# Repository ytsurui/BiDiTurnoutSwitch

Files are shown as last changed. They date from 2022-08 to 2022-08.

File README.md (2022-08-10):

# BiDi Turnout Switch

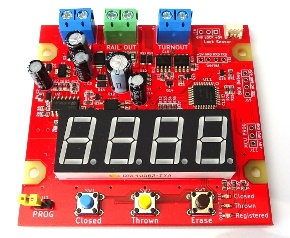
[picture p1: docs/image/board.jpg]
PCB Preview


NMRA DCC 規格のうち、BiDi (RailCom) によって送信される車両のアドレス情報を利用して、接続されているポイント線路を自動的に転換することが可能な装置です。

本リポジトリには、基板設計データとファームウェアが含まれます。

## 開発環境

- KiCad Version (5.1.12)-1
- Microchip Studio Version 7.0.2542

## 各種ドキュメント

  * [パーツリスト](docs/partslist.md)

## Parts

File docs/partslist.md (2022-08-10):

# Parts List

<table>
  <th>
    <td>Name</td>
    <td>Count</td>
  </th>
  <tr>
    <td>C1</td>
    <td>25PK220MEFC6.3X11<br>(220uF 25V)</td>
    <td>1</td>
  </tr>
  <tr>
    <td>C2, C3, C14</td>
    <td>25PK100MEFC5X11<br>(100uF 25V)</td>
    <td>3</td>
  </tr>
  <tr>
    <td>C12</td>
    <td>25PK470MEFC8X11.5<br>(470uF 25V)</td>
    <td>1</td>
  </tr>
  <tr>
    <td>C4, C11, C13</td>
    <td>GRM155F11E104ZA01<br>(0.1uF 25V 1005)</td>
    <td>3</td>
  </tr>
  <tr>
    <td>C15</td>
    <td>GRM155R11H103KA88<br>(0.01uF 50V 1005)</td>
    <td>1</td>
  </tr>
  <tr>
    <td>D1, D2</td>
    <td>SR54F</td>
    <td>2</td>
  </tr>
  <tr>
    <td>D3-D5</td>
    <td>1N4148W</td>
    <td>3</td>
  </tr>
  <tr>
    <td>D11-D14</td>
    <td>SS2040FL</td>
    <td>4</td>
  </tr>
  <tr>
    <td>D15</td>
    <td>OSL40562-IYA<br>(0.56 Inch Four Digit Display, Common Anode)</td>
    <td>1</td>
  </tr>
  <tr>
    <td>D16</td>
    <td>OSBL1608C1A<br>(Blue SMD LED, 1.6mm x 0.8mm)</td>
    <td>1</td>
  </tr>
  <tr>
    <td>D17</td>
    <td>OSYL1608C1A<br>(Yellow SMD LED, 1.6mm x 0.8mm</td>
    <td>1</td>
  </tr>
  <tr>
    <td>D18</td>
    <td>OSYG1608C1A<br>(Green SMD LED, 1.6mm x 0.8mm)</td>
    <td>1</td>
  </tr>
  <tr>
    <td>J1, J14</td>
    <td>TB111-2<br>(Screw Terminal, Blue)</td>
    <td>2</td>
  </tr>
  <tr>
    <td>J2</td>
    <td>TB111-2<br>(Screw Terminal, Green)</td>
    <td>1</td>
  </tr>
  <tr>
    <td>J17</td>
    <td>Molex 0530480350</td>
    <td>1</td>
  </tr>
  <tr>
    <td>Q1, Q2</td>
    <td>SSM3K7002BFU</td>
    <td>2</td>
  </tr>
  <tr>
    <td>Q11, Q12</td>
    <td>FDS4897C</td>
    <td>2</td>
  </tr>
  <tr>
    <td>Q13-Q15</td>
    <td>2SC4116</td>
    <td>3</td>
  </tr>
  <tr>
    <td>R1, R2</td>
    <td>3.6 ohm 3.2mm x 2.5mm</td>
    <td>2</td>
  </tr>
  <tr>
    <td>R3, R4</td>
    <td>220 ohm 1.6mm x 0.8mm</td>
    <td>2</td>
  </tr>
  <tr>
    <td>R5</td>
    <td>270k ohm 1.6mm x 0.8mm</td>
    <td>1</td>
  </tr>
  <tr>
    <td>R7</td>
    <td>820 ohm 1.6mm x 0.8mm</td>
    <td>1</td>
  </tr>
  <tr>
    <td>R8</td>
    <td>33k ohm 1.6mm x 0.8mm</td>
    <td>1</td>
  </tr>
  <tr>
    <td>R6, R10, R15, R21, R22<br>R25, R26, R31-R37, R41</td>
    <td>1k ohm 1.6mm x 0.8mm</td>
    <td>15</td>
  </tr>
  <tr>
    <td>R11, R12</td>
    <td>10k ohm 1.6mm x 0.8mm</td>
    <td>2</td>
  </tr>
  <tr>
    <td>R9, R27, R28</td>
    <td>100k ohm 1.6mm x 0.8mm</td>
    <td>3</td>
  </tr>
  <tr>
    <td>R23, R24</td>
    <td>330 ohm 1.6mm x 0.8mm</td>
    <td>2</td>
  </tr>
  <tr>
    <td>R40-R42</td>
    <td>4.7k ohm 1.6mm x 0.8mm</td>
    <td>3</td>
  </tr>
  <tr>
    <td>SW1</td>
    <td>DTS-63-N-V-BLU<br>(Blue Tact Switch)</td>
    <td>1</td>
  </tr>
  <tr>
    <td>SW2</td>
    <td>DTS-63-N-V-YLW<br>(Yellow Tact Switch)</td>
    <td>1</td>
  </tr>
  <tr>
    <td>SW3</td>
    <td>DTS-63-N-V-BLK<br>(Black Tact Switch)</td>
    <td>1</td>
  </tr>
  <tr>
    <td>U1, U12</td>
    <td>NJM78L05UA<br>(5V 100mA)</td>
    <td>2</td>
  </tr>
  <tr>
    <td>U2</td>
    <td>LM339<br>(SOIC14)</td>
    <td>1</td>
  </tr>
  <tr>
    <td>U11</td>
    <td>ATmega808-AU<br>ATmega808-AF</td>
    <td>1</td>
  </tr>
  <tr>
    <td>U13</td>
    <td>TLP2361</td>
    <td>1</td>
  </tr>
</table>

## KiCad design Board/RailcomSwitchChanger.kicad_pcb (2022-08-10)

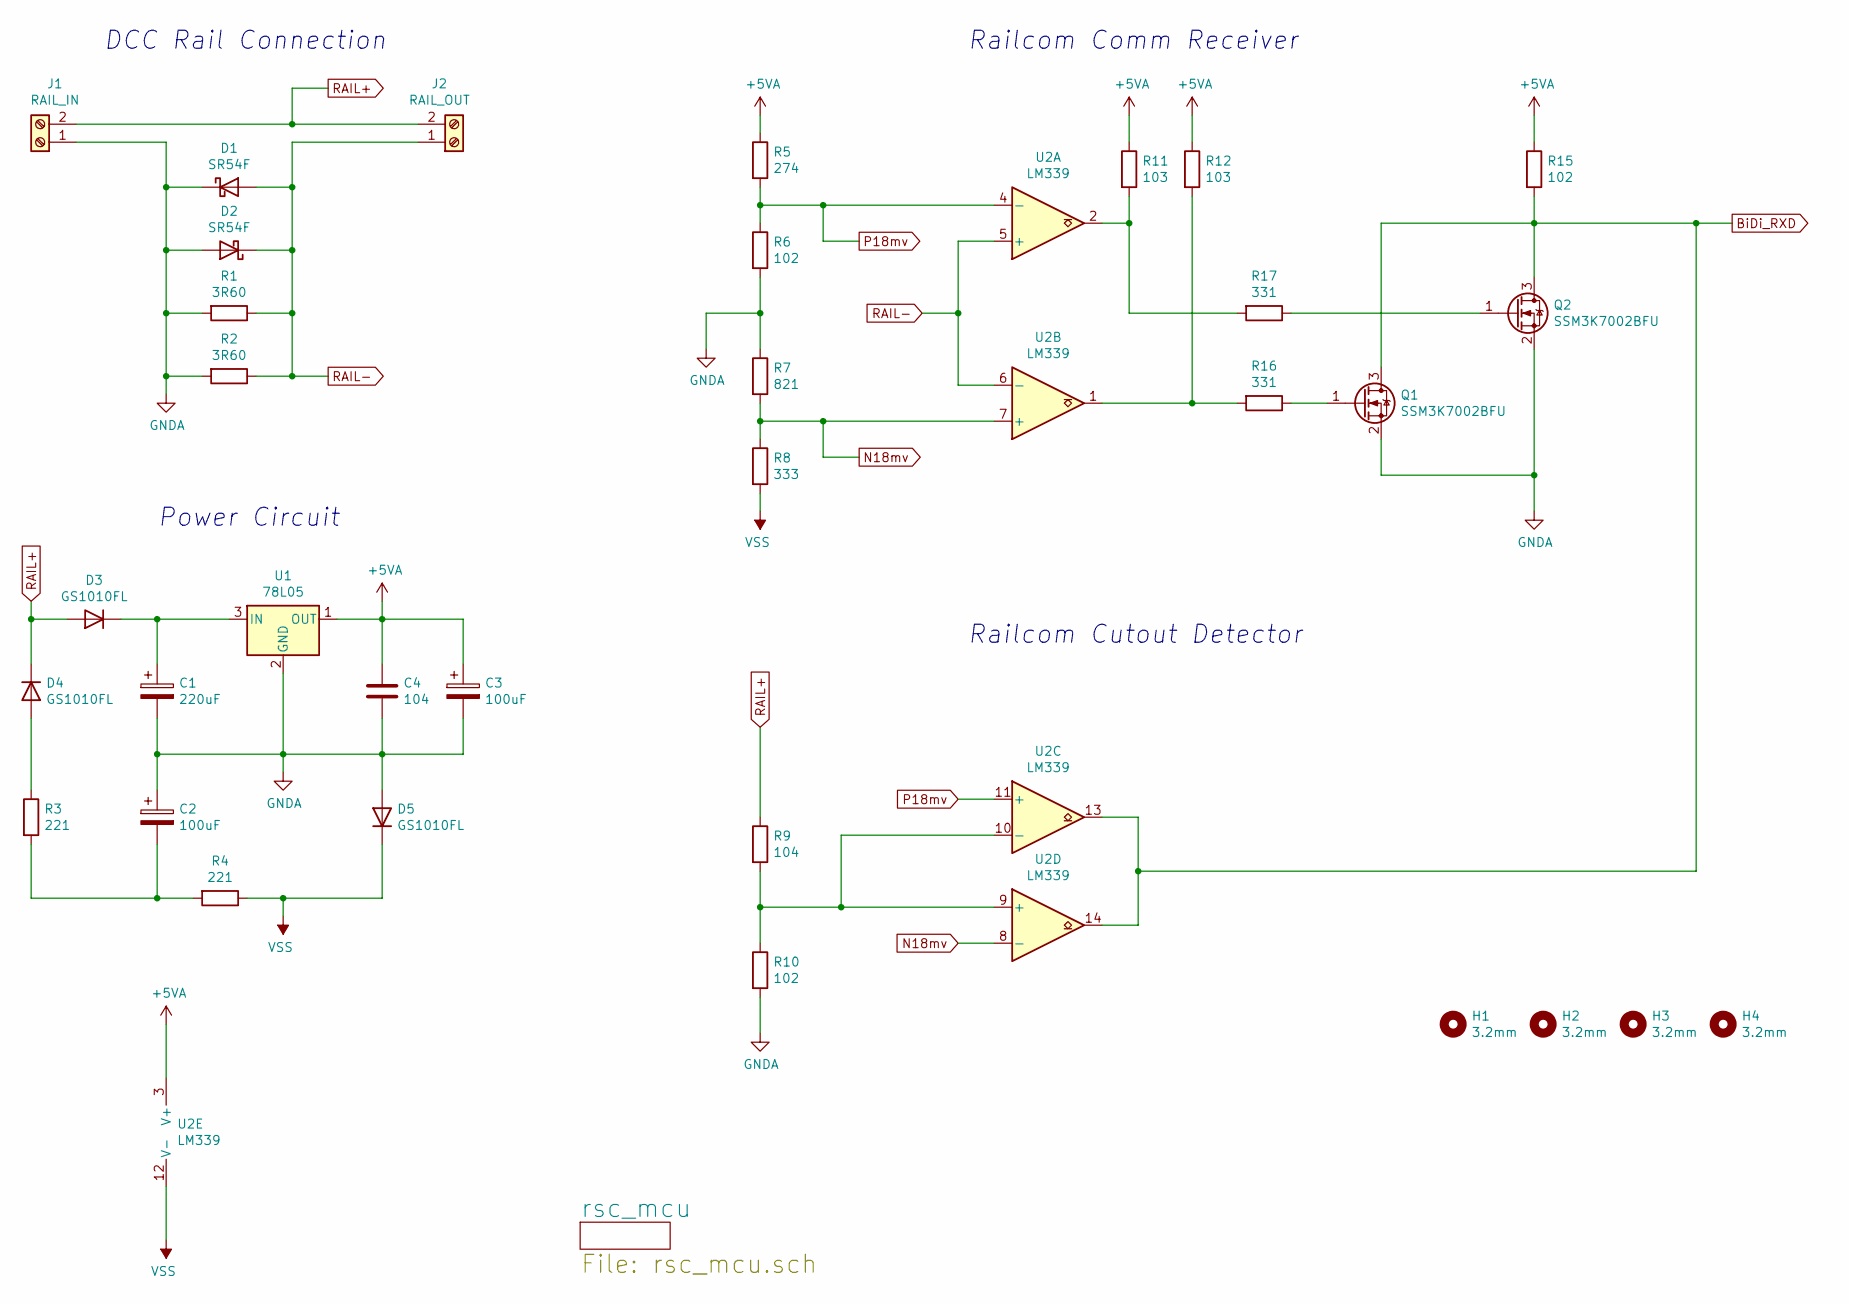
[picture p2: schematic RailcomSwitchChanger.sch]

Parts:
C1: 220uF; CAP_TH_6.3x11
C2, C3: 100uF; CAP_TH_5x11
C4: 104; C_1005
D1, D2: SR54F; SMBF
D3, D4, D5: GS1010FL; SOD-123FL
H1, H2, H3, H4: 3.2mm; HOLE_3.2mm
J1: RAIL_IN; TB111-2
J2: RAIL_OUT; TB111-2
Q1, Q2: SSM3K7002BFU; SC-70
R1, R2: 3R60; R_3225
R3, R4: 221; R_1608
R5: 274; R_1608
R6, R10, R15: 102; R_1608
R7: 821; R_1608
R8: 333; R_1608
R9: 104; R_1608
R11, R12: 103; R_1608
R16, R17: 331; R_1608
U1: 78L05; SOT-89-3
U2: LM339; SOIC-14

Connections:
+5VA: C3.1, C4.1, R5.1, R11.1, R12.1, R15.1, U1.1 (OUT), U2.3 (V+)
BiDi_RXD: Q1.3 (D), Q2.3 (D), R15.2, U2.13, U2.14; also elsewhere on the board
GNDA: C1.2, C2.1, C3.2, C4.2, D1.1 (K), D2.2 (A), D5.2 (A), J1.1, Q1.2 (S), Q2.2 (S), R1.2, R2.2, R6.2, R7.1, R10.2, U1.2 (GND); also elsewhere on the board
N18mv: R7.2, R8.1, U2.7 (+), U2.8 (-)
unnamed: C1.1, D3.1 (K), U1.3 (IN)
unnamed: C2.2, R3.2, R4.2
unnamed: D4.2 (A), R3.1
unnamed: Q1.1 (G), R16.1
unnamed: Q2.1 (G), R17.1
unnamed: R9.2, R10.1, U2.9 (+), U2.10 (-)
unnamed: R11.2, R17.2, U2.2
unnamed: R12.2, R16.2, U2.1
P18mv: R5.2, R6.1, U2.4 (-), U2.11 (+)
RAIL+: D3.2 (A), D4.1 (K), J1.2, J2.2, R9.1; also elsewhere on the board
RAIL-: D1.2 (A), D2.1 (K), J2.1, R1.1, R2.1, U2.5 (+), U2.6 (-)
VSS: D5.1 (K), R4.1, R8.2, U2.12 (V-)

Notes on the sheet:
Railcom Cutout Detector
Power Circuit
DCC Rail Connection
Railcom Comm Receiver

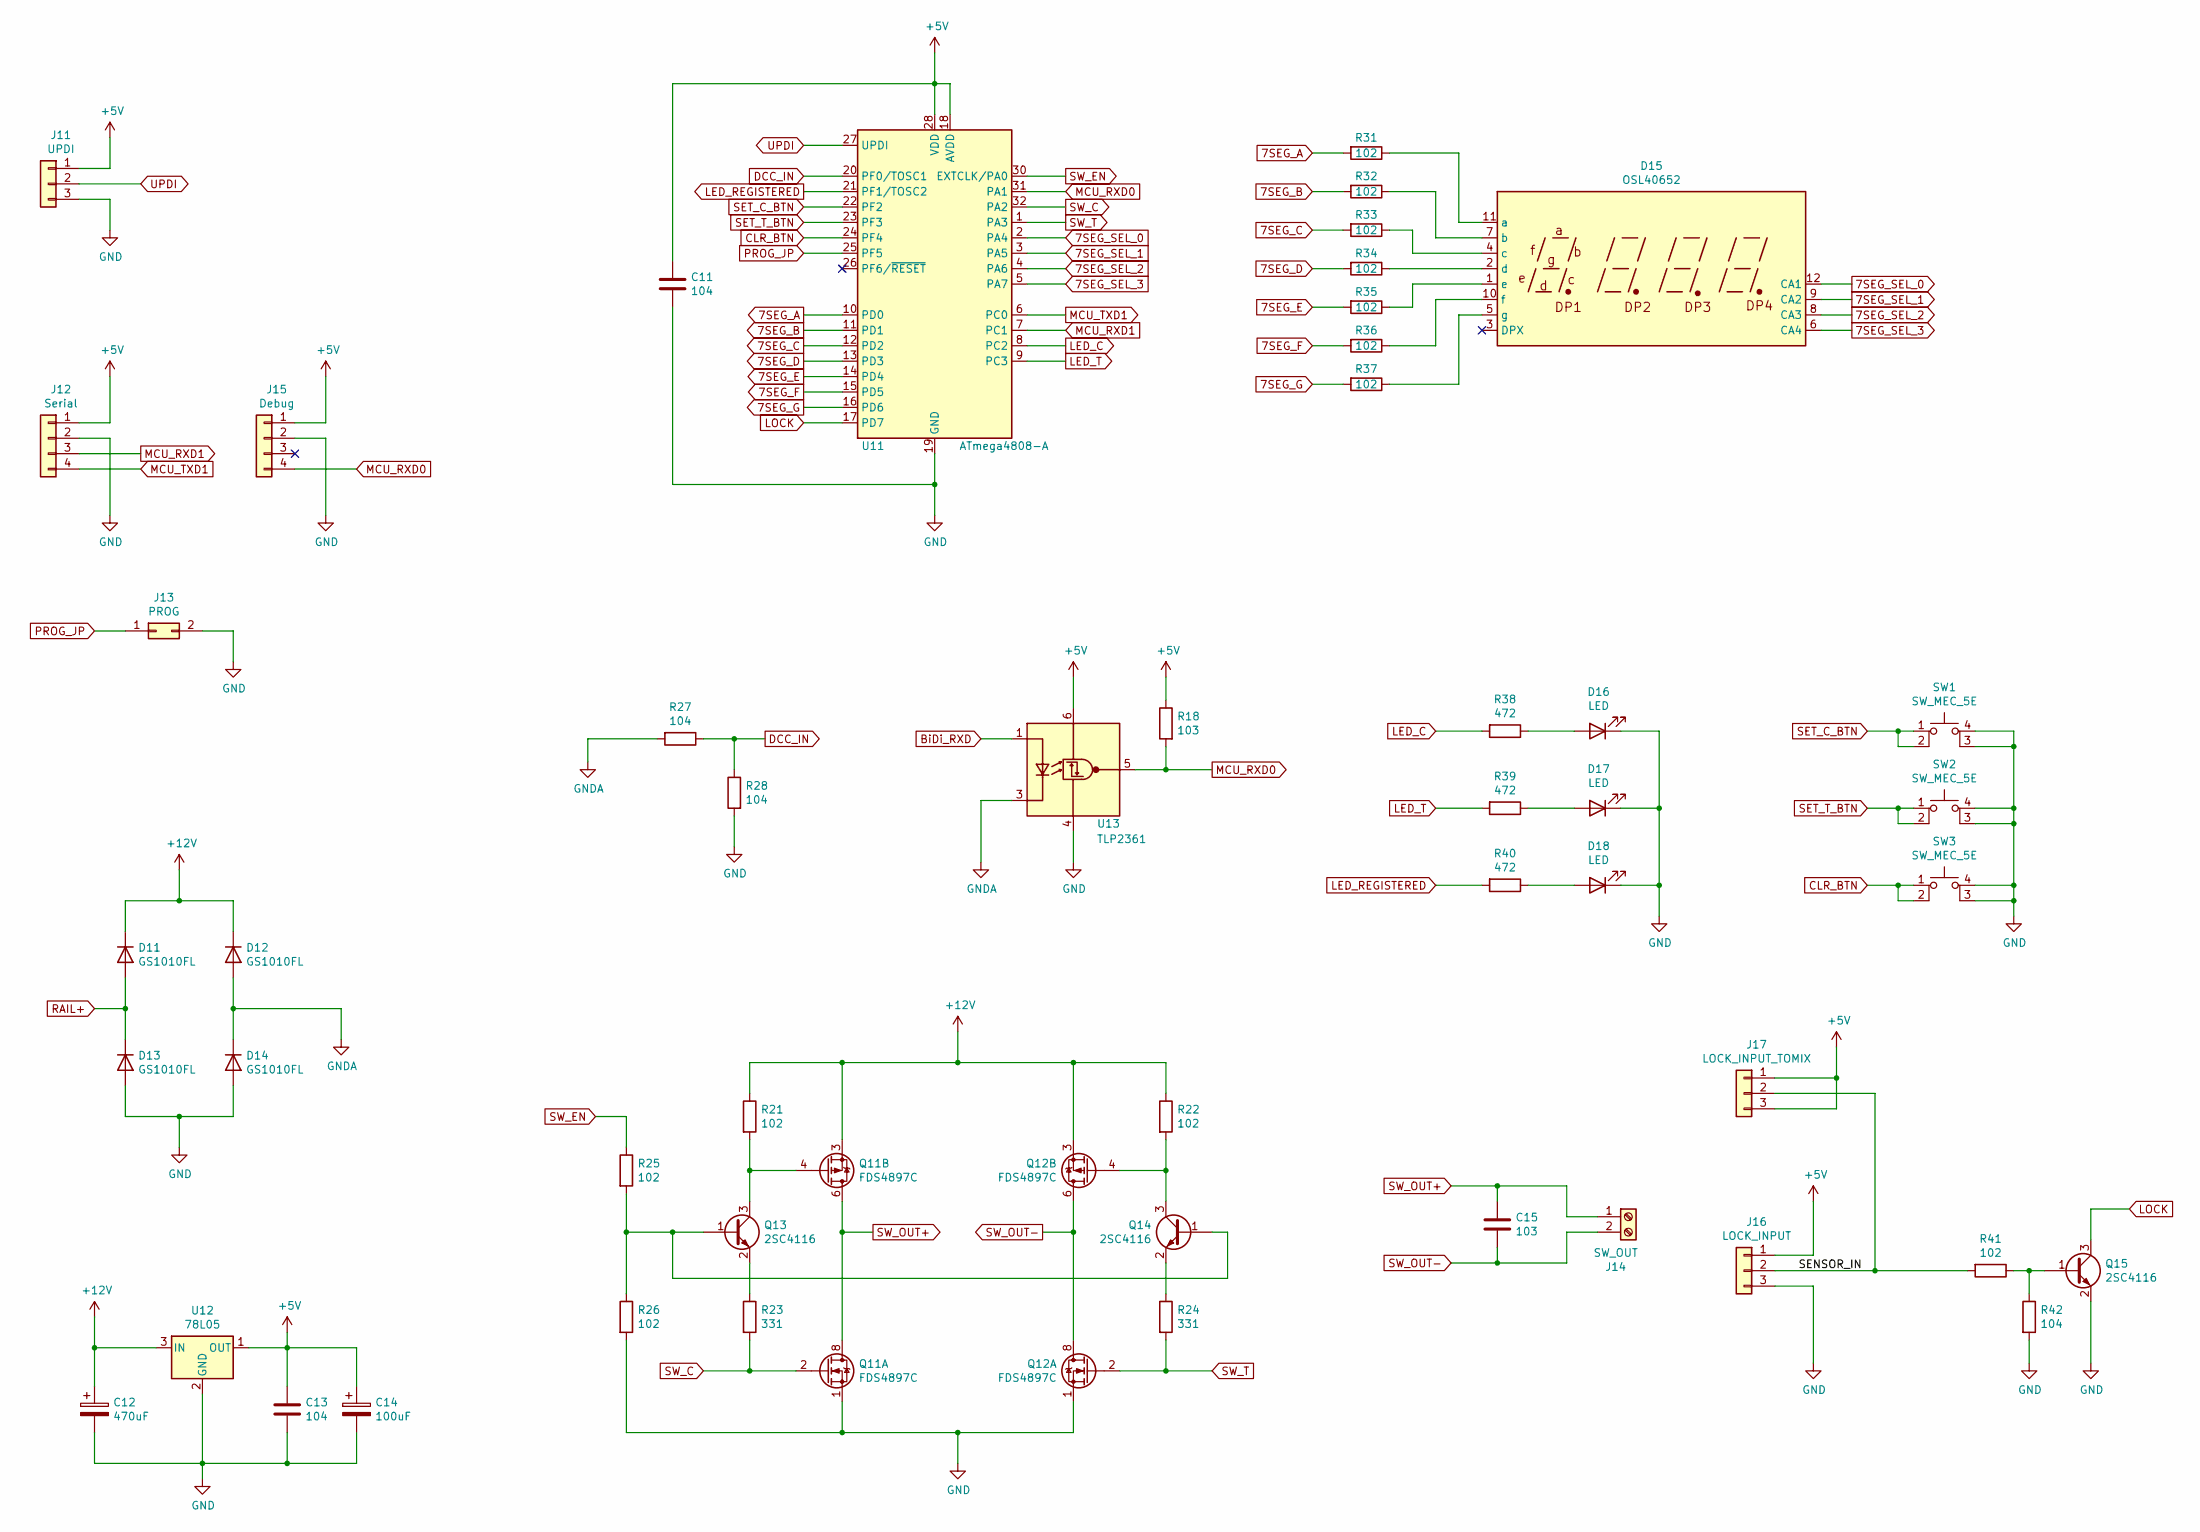
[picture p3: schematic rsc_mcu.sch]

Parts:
C11, C13: 104; C_1005
C12: 470uF; CAP_TH_8x11_5
C14: 100uF; CAP_TH_5x11
C15: 103; C_1005
D11, D12, D13, D14: GS1010FL; SOD-123FL
D15: OSL40652; OSL40562
D16, D17, D18: LED; LED_1608
J11: UPDI; PinHeader_01x03
J12: Serial; pin_array_1x4
J13: PROG; pin_array_1x2
J14: SW_OUT; TB111-2
J15: Debug; pin_array_1x4
J16: LOCK_INPUT; PinHeader_01x03
J17: LOCK_INPUT_TOMIX; Molex_0530480350
Q11, Q12: FDS4897C; SO-8
Q13, Q14, Q15: 2SC4116; SC-70
R18: 103; R_1608
R21, R22, R25, R26, R31, R32, R33, R34, R35, R36, R37, R41: 102; R_1608
R23, R24: 331; R_1608
R27, R28, R42: 104; R_1608
R38, R39, R40: 472; R_1608
SW1, SW2, SW3: SW_MEC_5E; TS-0606
U11: ATmega4808-A; TQFP-32_7x7mm_P0.8mm
U12: 78L05; SOT-89-3
U13: TLP2361; SO-6_5pin

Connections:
7SEG_A: R31.2, U11.10 (PD0)
7SEG_B: R32.2, U11.11 (PD1)
7SEG_C: R33.2, U11.12 (PD2)
7SEG_D: R34.2, U11.13 (PD3)
7SEG_E: R35.2, U11.14 (PD4)
7SEG_F: R36.2, U11.15 (PD5)
7SEG_G: R37.2, U11.16 (PD6)
7SEG_SEL_0: D15.12 (CA1), U11.2 (PA4)
7SEG_SEL_1: D15.9 (CA2), U11.3 (PA5)
7SEG_SEL_2: D15.8 (CA3), U11.4 (PA6)
7SEG_SEL_3: D15.6 (CA4), U11.5 (PA7)
+5V: C11.1, C13.1, C14.1, J11.1, J12.1, J15.1, J16.1, J17.1, J17.3, R18.1, U11.18 (AVDD), U11.28 (VDD), U12.1 (OUT), U13.6 (VDD)
+12V: C12.1, D11.1 (K), D12.1 (K), Q11.3 (1), Q12.3 (1), R21.1, R22.1, U12.3 (IN)
/rsc_mcu/SENSOR_IN: J16.2, J17.2, R41.2
BiDi_RXD: U13.1 (A); also elsewhere on the board
CLR_BTN: SW3.1, SW3.2, U11.24 (PF4)
DCC_IN: R27.1, R28.1, U11.20 (PF0/TOSC1)
GND: C11.2, C12.2, C13.2, C14.2, D13.2 (A), D14.2 (A), D16.1 (K), D17.1 (K), D18.1 (K), J11.3, J12.2, J13.2, J15.2, J16.3, Q11.1 (S), Q12.1 (S), Q15.2 (E), R26.2, R28.2, R42.2, SW1.3 (K), SW1.4 (A), SW2.3 (K), SW2.4 (A), SW3.3 (K), SW3.4 (A), U11.19 (GND), U11.29 (GND), U12.2 (GND), U13.4 (GND)
GNDA: D12.2 (A), D14.1 (K), R27.2, U13.3 (K); also elsewhere on the board
LED_C: R38.2, U11.8 (PC2)
LED_REGISTERED: R40.2, U11.21 (PF1/TOSC2)
LED_T: R39.2, U11.9 (PC3)
LOCK: Q15.3 (C), U11.17 (PD7)
MCU_RXD0: J15.4, R18.2, U11.31 (PA1), U13.5 (VO)
MCU_RXD1: J12.3, U11.7 (PC1)
MCU_TXD1: J12.4, U11.6 (PC0)
unnamed: D15.1 (e), R35.1
unnamed: D15.2 (d), R34.1
unnamed: D15.4 (c), R33.1
unnamed: D15.5 (g), R37.1
unnamed: D15.7 (b), R32.1
unnamed: D15.10 (f), R36.1
unnamed: D15.11 (a), R31.1
unnamed: D16.2 (A), R38.1
unnamed: D17.2 (A), R39.1
unnamed: D18.2 (A), R40.1
unnamed: Q11.4 (G), Q13.3 (C), R21.2
unnamed: Q12.4 (G), Q14.3 (C), R22.2
unnamed: Q13.1 (B), Q14.1 (B), R25.2, R26.1
unnamed: Q13.2 (E), R23.1
unnamed: Q14.2 (E), R24.1
unnamed: Q15.1 (B), R41.1, R42.1
PROG_JP: J13.1, U11.25 (PF5)
RAIL+: D11.2 (A), D13.1 (K); also elsewhere on the board
SET_C_BTN: SW1.1, SW1.2, U11.22 (PF2)
SET_T_BTN: SW2.1, SW2.2, U11.23 (PF3)
SW_C: Q11.2 (G), R23.2, U11.32 (PA2)
SW_EN: R25.1, U11.30 (EXTCLK/PA0)
SW_OUT+: C15.1, J14.1, Q11.5 (D), Q11.6 (D), Q11.7 (D), Q11.8 (D)
SW_OUT-: C15.2, J14.2, Q12.5 (D), Q12.6 (D), Q12.7 (D), Q12.8 (D)
SW_T: Q12.2 (G), R24.2, U11.1 (PA3)
UPDI: J11.2, U11.27 (UPDI)

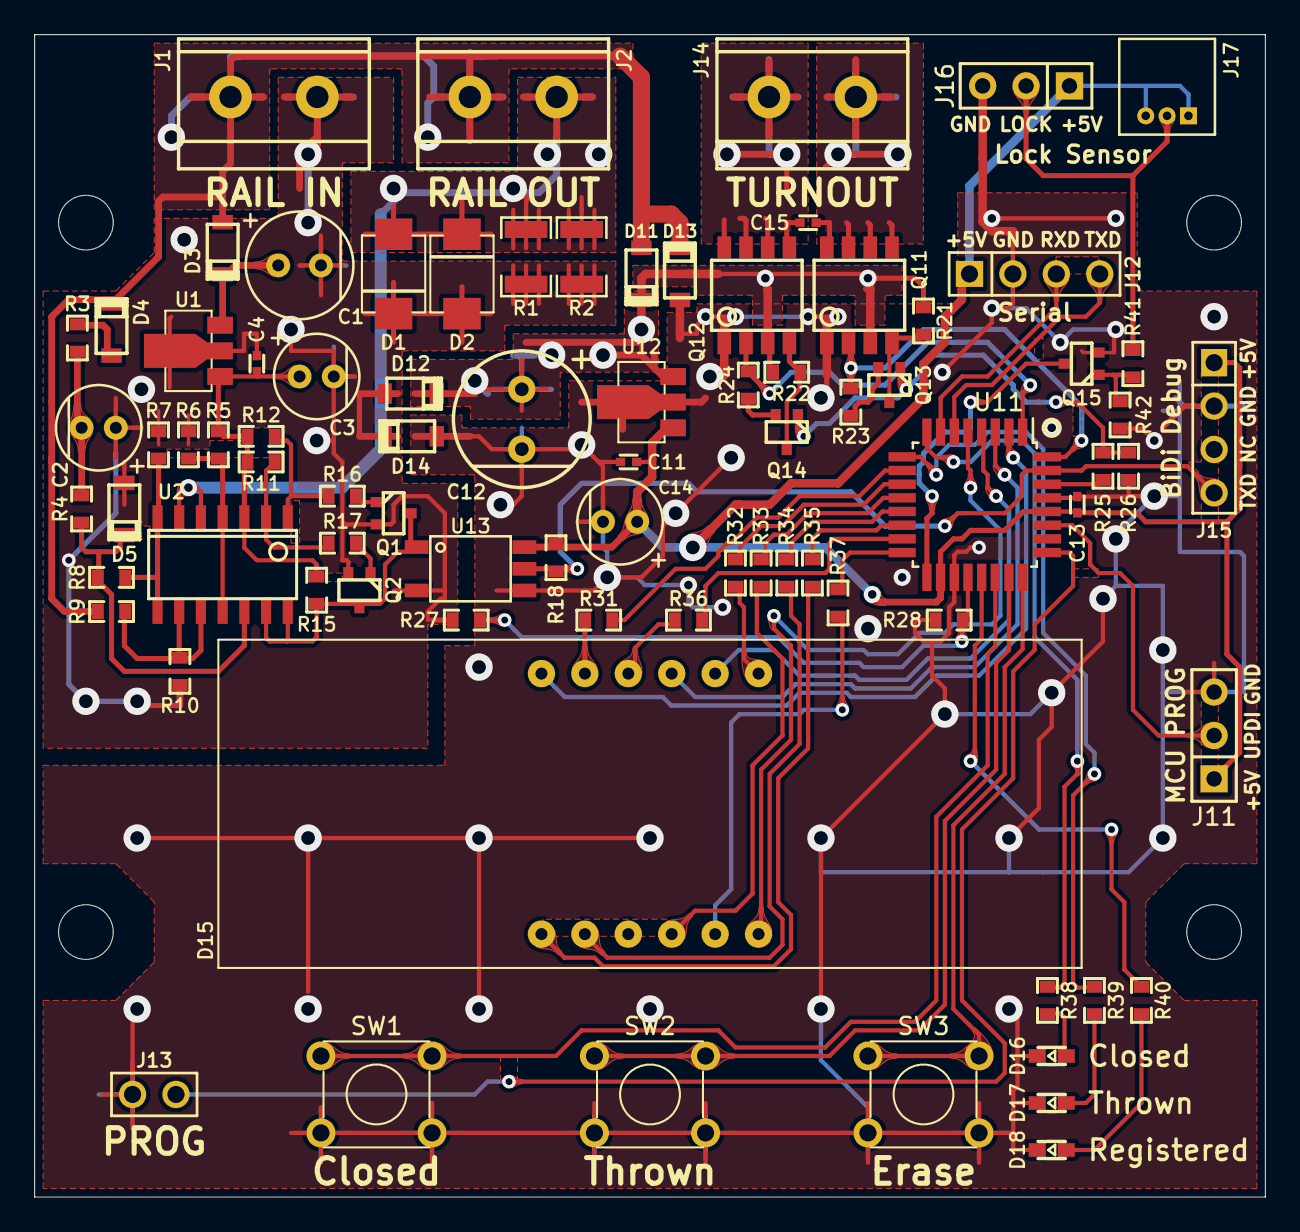
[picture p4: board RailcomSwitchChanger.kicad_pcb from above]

Board: 2 copper layers, 72.0 x 68.0 mm, 86 parts (0 on the bottom side), 65 nets.

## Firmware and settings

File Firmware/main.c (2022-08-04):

/*
 * main.c
 *
 * Created: 2021/12/31 0:07:21
 * Author : ytsurui
 */ 

#include <avr/io.h>
#include <util/delay.h>
#include <avr/interrupt.h>

#include "cpuclk.h"
#include "rtc.h"
#include "usart_railcom.h"
#include "railcom_recv.h"
#include "display_controller.h"
#include "pushButton.h"
#include "turnoutDriver.h"
#include "trainaddrStorage.h"
#include "turnoutaddrStorage.h"
#include "dcc_input.h"
#include "lock_sensor.h"

#define NO_RAILCOM_COUNT_MAX 2000

void delay_ms(uint8_t ms) {
	while(ms--) {
		_delay_ms(1);
	}
}

void progSwAddr(uint16_t addr, uint8_t stat) {
	static uint16_t addrCache;
	static uint8_t lastStat;
	//return;
	
	if ((addr == 0) || (addr > 2048)) return;
	
	if ((addr == addrCache) && (lastStat != stat)) {
		writeTurnoutAddr(addr);
		set_7seg_data(addr);
	} else {
		addrCache = addr;
		lastStat = stat;
	}
}

void moveSwitchFromAccPacket(uint16_t addr, uint8_t stat) {
	uint16_t swAddr;
	swAddr = getTurnoutAddr();
	
	if ((swAddr == 0) || (swAddr > 2048)) return;
	
	if (addr == swAddr) {
		if (stat) {
			// closed
			setTurnout(TURNOUT_CLOSE);
		} else {
			// thrown
			setTurnout(TURNOUT_THROWN);
		}
	}
}

int main(void)
{
	//uint8_t count1 = 0;
	
	uint8_t dccRecvPacketCache[48];
	uint8_t dccRecvPacketLength;
	
	uint16_t noRailcomCounter = 0;
	uint16_t railcomFlushCount = 0;
	
	uint16_t swAddr;
	
	uint16_t trainAddr;
	
	uint8_t swMove;
	uint16_t clrCount;
	
	uint8_t initCount = 0;
	
	setSwitchCallback(moveSwitchFromAccPacket);
	
	setCLK();
	initRTC();
	initUART0();
	//initUART1();
	initTrainAddrStorage();
	initTurnoutAddrStorage();
	
	initDisplay();
	initButton();
	initTurnoutDriver();
	initLockSensor();
	initDCCinput();
	
	PORTC.DIR = 0x0C;
	PORTF.DIR |= 0x02;
	
	sei();
	
	while (1) {
		if (chkRTCflag()) {
			initCount++;
			buttonClock();
			displayClock();
			
			if (initCount > 100) {
				break;
			}
		}
		
		if (getButtonStat(BUTTON_ID_PROG)) {
			// Prog Mode
			initCount = 0xFF;
			break;
		}
	}
	
	if (initCount == 0xFF) {
		// Prog Mode
		set_prog_mode();
		setSwitchCallback(progSwAddr);
		clrCount = 0;
		
		while (1) {
			dccPacketShifter(&dccRecvPacketLength, dccRecvPacketCache);
			if (dccRecvPacketLength) {
				dccPacketRouter(dccRecvPacketLength, dccRecvPacketCache);
				dccRecvPacketLength = 0;
			}
			
			if (chkRTCflag()) {
				displayClock();
				buttonClock();
				
				if ((clrCount != 0) && (clrCount < 1000)) {
					clrCount++;
				}
			}
			
			if (getButtonStat(BUTTON_ID_CLR)) {
				// Long-Push Clear
				//clrCount++;
				if (clrCount == 0) {
					clrCount = 1;
				}
			} else {
				clrCount = 0;
			}
			
			if (clrCount >= 1000) {
				set_clr_msg();
				writeTurnoutAddr(0);
				clearAddrStorageRaw();
			}
			
		}
	}
	
	swAddr = getTurnoutAddr();
	if ((swAddr != 0) && (swAddr <= 2048)) {
		set_7seg_data(swAddr);
	}
	
	//if (getTurnoutAddr() != 0) {
	//	set_7seg_data(getTurnoutAddr());
	//}
	
	setSwitchCallback(moveSwitchFromAccPacket);
	
    while (1) 
    {
		dccPacketShifter(&dccRecvPacketLength, dccRecvPacketCache);
		if (dccRecvPacketLength) {
			dccPacketRouter(dccRecvPacketLength, dccRecvPacketCache);
			dccRecvPacketLength = 0;
		}
		
		if (chkRTCflag()) {
			// 1ms Timer
			lockSensorClock();
			displayClock();
			buttonClock();
			turnoutClock();
			
			timeoutCountup();
			
			if (lockSensorStat()) {
				// Turnout Lock	
				resetTurnoutTimer();
			}
			
			if (noRailcomCounter < NO_RAILCOM_COUNT_MAX) {
				noRailcomCounter++;	
				if (addrViewTimeout()) {
					set_led_power_stat(0);
					railcomFlushCount++;
					if (railcomFlushCount == 256) {
						set_null_msg(0);
					} else if (railcomFlushCount == 512) {
						set_null_msg(1);
					} else if (railcomFlushCount == 768) {
						set_null_msg(2);
					} else if (railcomFlushCount == 1024) {
						set_null_msg(3);
						railcomFlushCount = 0;
					} else if (railcomFlushCount > 1024) {
						railcomFlushCount = 0;
					}
				}
			} else {
				railcomFlushCount++;
				if (railcomFlushCount == 256) {
					set_led_power_stat(0);
					set_null_msg(0);
				} else if (railcomFlushCount == 512) {
					set_led_power_stat(1);
					railcomFlushCount = 0;
				} else if (railcomFlushCount > 512) {
					railcomFlushCount = 0;
				}
			}
			
			
		}
		
		
		while (UART0recvSize()) {
			RailcomByteReceive(UART0GetData());
			noRailcomCounter = 0;
		}
		
		if (trainAddrRecvStat()) {
			trainAddr = getTrainAddr();
			set_led_power_stat(0);
			
			if (trainAddr != 0) {
				set_7seg_data(trainAddr);
			}
			
			swMove = scanAddrStorage(trainAddr);
			if (swMove > 0) {
				if (swMove & TRAINSTORAGE_REGISTERED) {
					PORTF.OUTSET = 0x02; 
				} else {
					PORTF.OUTCLR = 0x02;
				}
				setTurnout(swMove & 0x03);
			} else {
				PORTF.OUTCLR = 0x02;
			}
			
		}
		
		if (pushButtonEvent(BUTTON_ID_SET_C)) {
			//PORTC.OUTTGL = 0x04;
			if (getButtonStat(BUTTON_ID_SET_C)) {
				trainAddr = getTrainAddr();
				swMove = setAddrStorage(trainAddr, 1);
				if (swMove == TRAINSTORAGE_WRITE_SUCCESS) {
					setTurnout(TURNOUT_CLOSE);
					//if (trainAddr > 0) {
						PORTF.OUTSET = 0x02;
					//}
				}
			}
		}
		
		if (pushButtonEvent(BUTTON_ID_SET_T)) {
			//PORTC.OUTTGL = 0x08;
			if (getButtonStat(BUTTON_ID_SET_T)) {
				trainAddr = getTrainAddr();
				swMove = setAddrStorage(getTrainAddr(), 2);
				if (swMove == TRAINSTORAGE_WRITE_SUCCESS) {
					setTurnout(TURNOUT_THROWN);
					//if (trainAddr > 0) {
						PORTF.OUTSET = 0x02;
					//}
				}
			}
		}
		
		if (pushButtonEvent(BUTTON_ID_CLR)) {
			//PORTF.OUTTGL = 0x02;
			if (getButtonStat(BUTTON_ID_CLR)) {
				PORTF.OUTCLR = 0x02;
				if (clearAddrStorage(getTrainAddr())) {
					//swMove = scanAddrStorage(0);
					//if (swMove > 0) {
					//	setTurnout(swMove & 0x03);
					//}
				}
			}
		}
		
		
		
		
		//delay_ms(200);
		//PORTC.OUTTGL |= 0x0C;
    }
}

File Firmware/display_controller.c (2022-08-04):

/*
 * display_controller.c
 *
 * Created: 2021/12/31 0:49:56
 *  Author: Y.Tsurui
 */ 

#include <avr/io.h>
#include <avr/interrupt.h>
#include <avr/pgmspace.h>

#include "display_controller.h"

#define LED_A 0x01
#define LED_B 0x02
#define LED_C 0x04
#define LED_D 0x08
#define LED_E 0x10
#define LED_F 0x20
#define LED_G 0x40

uint8_t data_cache[4];
uint8_t select_flag = 0;

uint8_t power_flag = 0;

uint8_t appTimerFlag = 0;

//7-seg LED Port Assign
/*
A: PD0
B: PD1
C: PD2
D: PD3
E: PD4
F: PD5
G: PD6

CA1: PA4
CA2: PA5
CA3: PA6
CA4: PA7
*/

void set_port(uint8_t dec);

/*
ISR(TIMER1_COMPA_vect)
{
	appTimerFlag = 1;
	
	PORTD &= 0b11000011;
	
	if (power_flag) {
		PORTB &= 0x80;
		return;
	} else {
		set_port(data_cache[select_flag]);
		select_flag++;
	}	
	
	if (select_flag == 1) {
		PORTD |= 0b00000100;
	} else if (select_flag == 2) {
		PORTD |= 0b00010000;
	} else if (select_flag == 3) {
		PORTD |= 0b00100000;
	} else {
		PORTD |= 0b00001000;
		select_flag = 0;
	}
}

void set_7seg_timer(void)
{
	TCCR1A = 0b00000000;
	TCCR1B = 0b00001011;
	OCR1A = 128;
	OCR1B = OCR1A / 2;
	
	TIMSK |= 0b01000000;
	
	sei();
}
*/

void initDisplay(void) {
	PORTA.DIR |= 0xF0;
	PORTD.DIR |= 0x7F;
}

void displayClock(void) {
	PORTA.OUTCLR = 0xF0;
	
	if (power_flag) {
		PORTD.OUTCLR = 0x7F;
		return;
	} else {
		set_port(data_cache[select_flag]);
		select_flag++;
	}
	
	if (select_flag == 1) {
		PORTA.OUTSET = 0x80;
	} else if (select_flag == 2) {
		PORTA.OUTSET = 0x40;
	} else if (select_flag == 3) {
		PORTA.OUTSET = 0x20;
	} else {
		PORTA.OUTSET = 0x10;
		select_flag = 0;
	}
	
}

const PROGMEM uint8_t led7segDataTable[17] = {
	~(LED_A | LED_B | LED_C | LED_D | LED_E | LED_F),			// 0
	~(LED_B | LED_C),											// 1
	~(LED_A | LED_B | LED_D | LED_E | LED_G),					// 2
	~(LED_A | LED_B | LED_C | LED_D | LED_G),					// 3
	~(LED_B | LED_C | LED_F | LED_G),							// 4
	~(LED_A | LED_C | LED_D | LED_F | LED_G),					// 5
	~(LED_A | LED_C | LED_D | LED_E | LED_F | LED_G),			// 6
	~(LED_A | LED_B | LED_C),									// 7
	~(LED_A | LED_B | LED_C | LED_D | LED_E | LED_F | LED_G),	// 8
	~(LED_A | LED_B | LED_C | LED_D | LED_F | LED_G),			// 9
	~(LED_A | LED_B | LED_E | LED_F | LED_G),					// P
	~(LED_E | LED_G),											// r
	~(LED_C | LED_D | LED_E | LED_G),							// o
	~(LED_A | LED_B | LED_C | LED_D | LED_F | LED_G),			// g
	~(LED_G),													// -
	~(LED_G | LED_D | LED_E),									// C
	~(LED_E | LED_F | LED_D)									// L
};


void set_port(uint8_t dec)
{
	uint8_t readCache;
		
	//PORTB |= 0b01111111;
	PORTD.OUTSET = 0x7F;
	
	if (dec == 0xFF) {
		return;
	}
	
	if (dec > 0x80) {
		dec -= 119;
		readCache = pgm_read_byte(&led7segDataTable[dec]);
		//PORTB &= readCache;
		PORTD.OUT &= readCache;
	}
	
	if (dec < 10) {
		readCache = pgm_read_byte(&led7segDataTable[dec]);
		//PORTB &= readCache;
		PORTD.OUT &= readCache;
	}
	
	/*
	if (dec == 0) {
		//A-B-C-D-E-F
		PORTB &= ~(LED_A | LED_B | LED_C | LED_D | LED_E | LED_F);
	} else if (dec == 1) {	
		//B-C
		PORTB &= ~(LED_B | LED_C);
	} else if (dec == 2) {	
		//A-B-D-E-G
		PORTB &= ~(LED_A | LED_B | LED_D | LED_E | LED_G);
	} else if (dec == 3) {	
		//A-B-C-D-G
		PORTB &= ~(LED_A | LED_B | LED_C | LED_D | LED_G);
	} else if (dec == 4) {	
		//B-C-F-G
		PORTB &= ~(LED_B | LED_C | LED_F | LED_G);
	} else if (dec == 5) {	
		//A-C-D-F-G
		PORTB &= ~(LED_A | LED_C | LED_D | LED_F | LED_G);
	} else if (dec == 6) {	
		//A-C-D-E-F-G
		PORTB &= ~(LED_A | LED_C | LED_D | LED_E | LED_F | LED_G);
	} else if (dec == 7) {	
		//A-B-C
		PORTB &= ~(LED_A | LED_B | LED_C);
	} else if (dec == 8) {	
		//A-B-C-D-E-F-G
		PORTB &= ~(LED_A | LED_B | LED_C | LED_D | LED_E | LED_F | LED_G);
	} else if (dec == 9) {	
		//A-B-C-D-F-G
		PORTB &= ~(LED_A | LED_B | LED_C | LED_D | LED_F | LED_G);
	} else if (dec == 0x81) {
		//P (A-B-E-F-G)
		PORTB &= ~(LED_A | LED_B | LED_E | LED_F | LED_G);
	} else if (dec == 0x82) {
		//R (A-E-F)
		PORTB &= ~(LED_A | LED_E | LED_F);
	} else if (dec == 0x83) {
		//O (A-B-C-D-E-F)
		PORTB &= ~(LED_A| LED_B | LED_C | LED_D | LED_E | LED_F);
	} else if (dec == 0x84) {
		//G (A-B-C-D-F-G)
		PORTB &= ~(LED_A | LED_B | LED_C | LED_D | LED_F | LED_G);
	}
	*/
	
}

void set_7seg_data(uint16_t data)
{
	uint8_t i;
	
	for (i = 0; i < 4; i++) {
		if ((data == 0) && (i != 0)) {
			data_cache[i] = 0xFF;
		} else {
			data_cache[i] = data % 10;
			data = data / 10;
		}
	}
}

void set_led_power_stat(uint8_t stat)
{
	power_flag = stat;
}

void set_prog_mode(void)
{
	data_cache[0] = 0x84;
	data_cache[1] = 0x83;
	data_cache[2] = 0x82;
	data_cache[3] = 0x81;
}

void set_clr_msg(void)
{
	data_cache[0] = 0x82;
	data_cache[1] = 0x87;
	data_cache[2] = 0x86;
	data_cache[3] = 0xFF;
}

void set_null_msg(uint8_t pos) {
	uint8_t i;
	
	for (i = 0; i < 4; i++) {
		if (i == pos) {
			data_cache[i] = 0x85;
		} else {
			data_cache[i] = 0xFF;
		}
	}
}

uint8_t appTimer(void) {
	if (appTimerFlag) {
		appTimerFlag = 0;
		return (1);
	}
	return (0);
}

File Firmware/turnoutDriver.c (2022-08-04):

/*
 * turnoutDriver.c
 *
 * Created: 2021/12/31 15:43:38
 *  Author: Y.Tsurui
 */

#include <avr/io.h>
#include "turnoutDriver.h"

uint8_t turnoutMoveStartFlag;
uint16_t turnoutCounter;
uint8_t turnoutMove;
uint8_t turnoutNowStat;

uint16_t turnoutLockCounter = 0;
#define TURNOUT_LOCK_MAX 3000;

uint8_t turnoutLockLEDcounter = 0;


void turnoutClock(void) {
	if (turnoutLockCounter > 0) {
		turnoutLockCounter--;
			
		
		if (turnoutLockCounter == 0) {
			if (turnoutNowStat == TURNOUT_CLOSE) {
				// LED Closed On
				PORTC.OUTSET = 0x04;
			} else if (turnoutNowStat == TURNOUT_THROWN) {
				// LED Thrown On
				PORTC.OUTSET = 0x08;
			}
			turnoutLockLEDcounter = 0;
		} else {
			turnoutLockLEDcounter++;
			if (turnoutLockLEDcounter == 0x3F) {
				if (turnoutNowStat == TURNOUT_CLOSE) {
					PORTC.OUTTGL = 0x04;
				} else if (turnoutNowStat == TURNOUT_THROWN) {
					PORTC.OUTTGL = 0x08;
				}
				turnoutLockLEDcounter = 0;
			}
		}
	}
	
	if (turnoutCounter == 0) {
		if (turnoutMoveStartFlag == 0) {
			return;
		}
		
		if (turnoutLockCounter != 0) {
			return;
		} 
		
		turnoutMove = turnoutMoveStartFlag;
		turnoutNowStat = turnoutMoveStartFlag;
		turnoutMoveStartFlag = 0;
		turnoutCounter = 1;
	}
	
	if (turnoutCounter == 1) {
		
		if (turnoutMove == TURNOUT_CLOSE) {
			PORTC.OUTSET = 0x04;
			PORTC.OUTCLR = 0x08;
		} else if (turnoutMove == TURNOUT_THROWN) {
			PORTC.OUTSET = 0x08;
			PORTC.OUTCLR = 0x04;
		} else {
			turnoutCounter = 0;
			turnoutMove = 0;
			return;
		}
	} else if (turnoutCounter < 1000) {
		if ((turnoutCounter & 0x007F) == 0x007F) {
			if (turnoutMove == TURNOUT_CLOSE) {
				PORTC.OUTTGL = 0x04;
				PORTC.OUTCLR = 0x08;
			} else if (turnoutMove == TURNOUT_THROWN) {
				PORTC.OUTTGL = 0x08;
				PORTC.OUTCLR = 0x04;
			}
		}
	} else if (turnoutCounter == 1001) {
		if (turnoutMove == TURNOUT_CLOSE) {
			PORTA.OUTSET = 0x05;
			PORTC.OUTSET = 0x04;
			PORTC.OUTCLR = 0x08;
		} else if (turnoutMove == TURNOUT_THROWN) {
			PORTA.OUTSET = 0x09;
			PORTC.OUTSET = 0x08;
			PORTC.OUTCLR = 0x04;
		} else {
			turnoutCounter = 0;
			turnoutMove = 0;
			return;
		}
		turnoutMove = 0;
	} else if (turnoutCounter == 1250) {
		PORTA.OUTCLR = 0x0D;
	} else if (turnoutCounter >= 2000) {
		if (turnoutMove > 0) {
			turnoutCounter = 1;
			return;
		}
		turnoutCounter = 0;
		return;
	}
	
	turnoutCounter++;
}

void initTurnoutDriver(void) {
	PORTA.DIRSET = 0x0D;	// output PA0,PA2,PA3
	PORTC.DIRSET = 0x0C;	// output PC2,PC3 (LED)
	turnoutCounter = 0;
}

void setTurnout(uint8_t dir) {
	//turnoutMove = dir;
	//if (turnoutCounter == 0) {
		//turnoutCounter = 1;
		//turnoutMoveStartFlag = 1;
	//}
	//turnoutMoveStartFlag = 1;
	turnoutMoveStartFlag = dir;
}

void resetTurnoutTimer(void) {
	turnoutLockCounter = TURNOUT_LOCK_MAX;
}
